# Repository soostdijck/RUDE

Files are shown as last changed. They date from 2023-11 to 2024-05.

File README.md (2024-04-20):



# Robak Unkillable Demon Edition

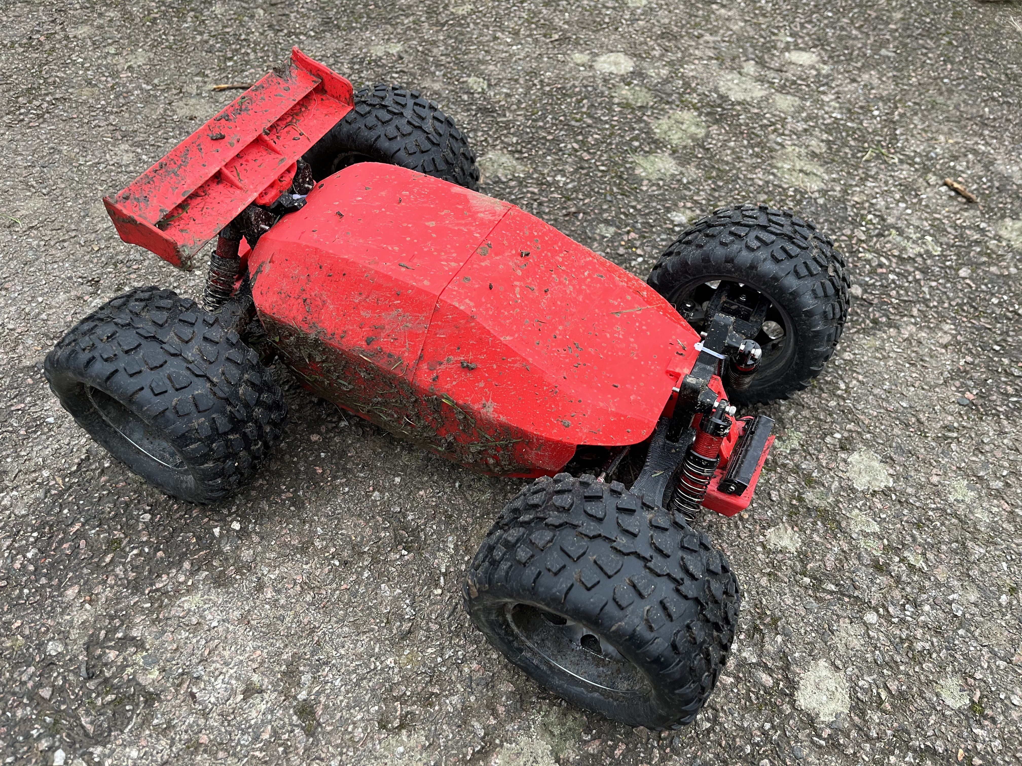
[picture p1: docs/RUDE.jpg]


Join the Discord (https://discord.gg/Cc8tsbZAE3)

An open-source RC car based on [Robak v2.2](https://github.com/robaki-dev/robak/).

The most resilient RC car on the planet! More driving and less repairing. This car only stops when your battery is empty. If you break this car after flying out of your apartment window I failed.

Select your own hardware with the BOM as your guide. All plastic parts can be 3D printed or bought from [my future webshop?]() (if you want to buy RUDE car parts, ask me in discord for now).

[Printing instructions](docs/printing.md)

[Bill Of Materials](docs/BOM.md)

[Assembly](docs/Assembly.md)

### FAQ: What is this car going to cost me?

Complete kit without plastic parts: Low budget: €200. Premium: €400. The BOM lists all premium parts.

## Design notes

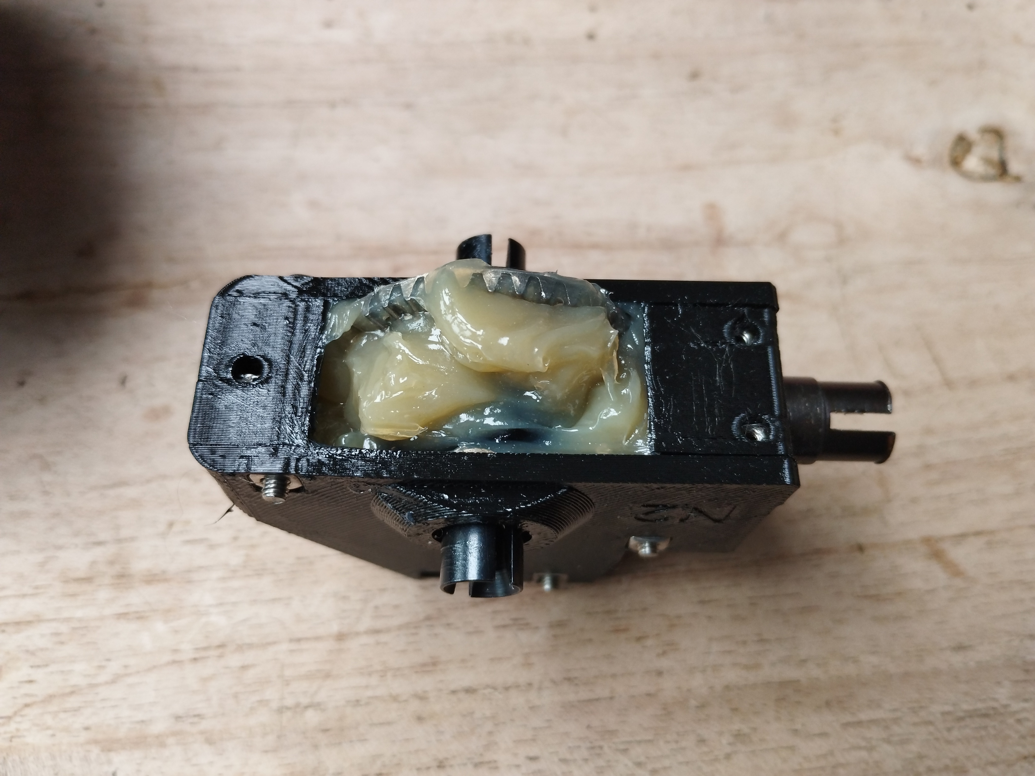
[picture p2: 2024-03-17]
docs/diff_housing_grease.jpg

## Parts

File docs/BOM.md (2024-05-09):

# BOM

Special attention to HSP 102011 and 2x190mm + 4x66mm ⌀5mm steel rods which are not included in stock Robak BOM. Also additional SHCS M3 + hex-nuts and 2x M5x40 bolts + square nuts are necessary if you come from Robak.

This car can handle much more power than Robak and is also heavier, I don't advise anything below 3S.

## Electronics

Part | Name | QTY | Notes
--- | --- | --- | ---
ESC + motor | 36xx or 42xx up to 82mm length | 1 | F.e. 3660 = 36mm diameter & 60mm length, 4278 = 42mm diameter & 78mm length.
ESC + motor | Hobbywing Ezrun MAX10 3665SD G3 2400KV + G2 140A ESC | 1 | Recommended. The newest Ezrun MAX8 & MAX10 sensored series are great. Get your Hobbywing electronics at a local shop, because aliexpress doesn't do warranty!
Battery for recommended MAX10 combo | 4S 4700mAh | 1 | https://s.click.aliexpress.com/e/_Dm7oLEB
RX + TX | DumboRC DDF-350 | X10FG or X6DCG | screen, lights/indicators support and with gyro https://s.click.aliexpress.com/e/_oCQUDqW (select M2 for metal steering wheel)
Servo | DS3240-180 or any other 180 deg variant | 1 | https://s.click.aliexpress.com/e/_DnBFawT
1:8 Motor | Ysido 4274 | 1 | Cheap but overpowered https://s.click.aliexpress.com/e/_DmBblkx NOTE: you need a 1:8 ESC for this. [has 6.5mm banana plugs instead of 4mm]
1:8 ESC | Hobbywing Quicrun 8BL150 | 1 | I use this in combination with the Ysido. Get your Hobbywing electronics at a local shop, because aliexpress doesn't do warranty!

## HSP

Part | Name | QTY | Notes
--- | --- | --- | ---
steering links | HSP 102011 | 2 | different from stock Robak
differential | HSP 02024 |2 | https://aliexpress.com/item/1178316591.html I recommend to get all your HSP parts from this store. Their quality seems to be superior. You can order, cancel payment, then ask seller to reduce the shipping costs.
front gear | HSP 02030 |1 |
rear gear | HSP 03015 |1 |e-clip shoud be included
cvd | HSP 108015 |4 |2 types available; more info on robaki.dev
5/6mm wheel hex | HSP 122042 |4 | https://s.click.aliexpress.com/e/_DnSrrOX depth depends a bit on the type of wheel. For the recommended wheels 5/6mm.
cups | HSP 02016 |2 |
servo link | HSP 02012 |1 |
steering links | HSP 06016 |1 |one pair
drive shaft | HSP 04003 |1 |
spur gear | HSP 11184 |1 |
pinion gear | HSP 11184 |1 | 29T ⌀3.175/5mm, check shaft of your motor. For weaker motors pick 21T.
ball head screw | HSP 02038 |4 |for steering
small bearings |5x10x4mm | 5pcs | https://s.click.aliexpress.com/e/_Ey7tCg3
big bearings |10x15x4mm | 4pcs | https://s.click.aliexpress.com/e/_oCNvIsS

### HSP must-have spares

Part | Name | QTY | Notes
--- | --- | --- | ---
differential | HSP 02024 | 2 |
front gear | HSP 02030 |1 |
rear gear | HSP 03015 |1 |e-clip shoud be included
cups | HSP 02016 |1 |
pinion gear | HSP 11184 |1 |⌀3.175/5mm, check shaft of your motor
grub screws | HSP 02099 |1 |
main gear pin | HSP 08027 |1 |
small bearings |5x10x4mm | 2 | 
big bearings |10x15x4mm | 2 | 

## Other

Part | Name | QTY | Notes
--- | --- | --- | ---
wheels | HSP 88005 | 4 | metal rims preferred since I have broken plastic rims before https://aliexpress.com/item/4000537479774.html [I haven't tried TPU wheels yet]
shocks |INJORA Aluminum Shock Absorber 100mm |4 | https://s.click.aliexpress.com/e/_EQmCy8T
battery straps |20mm width; 200mm long |2 |max width 25mm
DIY hinge pins |⌀5mm steel rod | 2x190mm + 4x66mm | https://s.click.aliexpress.com/e/_opSq9ew buying 500mm rods is best value [different from stock Robak]
sillicone oil (front & rear shocks) | 1000+ cSt | 20ml | this car's mass is >3kg so heavier oils preferred https://s.click.aliexpress.com/e/_ooUaPnU (very cheap, I'd recommend to buy both 2K and 1K)
sillicone oil (diffs) |80.000 cSt | 20ml |50.000-100.000 cSt will work https://s.click.aliexpress.com/e/_mKMass6 (from local shop is likely cheaper)
thread-locking fluid | | 10ml | Medium strength blue (cheap option: https://s.click.aliexpress.com/e/_mtYoqXC )
lithium grease | | 50ml |or any other grease for gears
CA glue / ZAP-RT | power glue | 20ml |tire glue (ZAP-RT for metal rims)

## Bolts

Part | Name | QTY | Notes
--- | --- | --- | ---
M5 Socket Head Screws | M5 SHCS 2x40 | | https://s.click.aliexpress.com/e/_mNYNVTc
M5 Square Nuts  | | 2 | https://s.click.aliexpress.com/e/_mKvxiiA
M3 Socket Head Screws | M3 SHCS 8x30 4x20 4x16 4x12 1x6 | | https://s.click.aliexpress.com/e/_mNYNVTc
M3 Flat Head Screws | M3 FHCS 30/25/20/16/12mm |20pcs each | https://s.click.aliexpress.com/e/_ontwkaW
M3 Thin Square Nuts  |DIN 562 |50 |ht. 1.8mm https://s.click.aliexpress.com/e/_mKvxiiA
M3 Nylon-Insert Locknuts |DIN 985; ISO 10511 |12 | for arm hinges https://s.click.aliexpress.com/e/_mKRqmKW
M3 General Purpose Washers |DIN 125; ISO 7089 |3 |motor mount to the plate https://s.click.aliexpress.com/e/_ooqqPiE
M4 Nylon-Insert Locknuts |DIN 985; ISO 10511 |4 |for wheels https://s.click.aliexpress.com/e/_mKRqmKW
M4 General Purpose Washers |DIN 125; ISO 7089 |4 |for wheels https://s.click.aliexpress.com/e/_ooqqPiE

## For stock body

Part | Name | QTY | Notes
--- | --- | --- | ---
M2x10mm Socket Head Screws |DIN 912; ISO 4762 |10 |bolt 2 body parts together https://s.click.aliexpress.com/e/_mKoi8nC 
M2 Nylon-Insert Locknuts |DIN 985; ISO 10511 |10 |bolt 2 body parts together https://s.click.aliexpress.com/e/_mKRqmKW
M8x60 bolt full thread |  |1 | Full Thread! To bolt rear body part to car. https://s.click.aliexpress.com/e/_EJMfISf 
M8 flange lock nut |  |1 | https://s.click.aliexpress.com/e/_Ew4tm55
M8 wing nut |  |1 | https://s.click.aliexpress.com/e/_EwzpS4j

## Tools

Part | Name | QTY | Notes
--- | --- | --- | ---
Worx electric screwdriver | WX242 | 1 | https://s.click.aliexpress.com/e/_msPBlN0 
Allen bits | H2 | 2 | https://s.click.aliexpress.com/e/_EuJdN3h or https://s.click.aliexpress.com/e/_msWyGcO

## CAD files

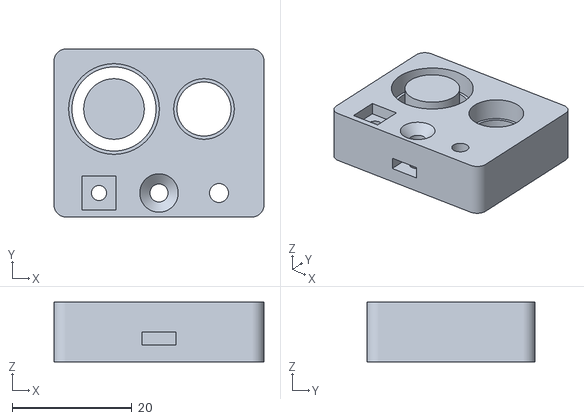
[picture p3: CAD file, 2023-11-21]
Calibration.stl
35.0 x 28.0 x 10.0

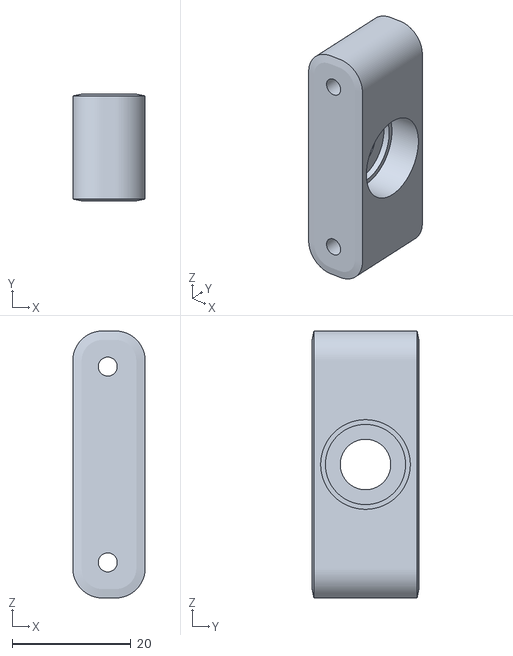
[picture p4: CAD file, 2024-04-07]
ROBAK_STL/CarrierHubR.stl
12.2 x 18.0 x 45.0

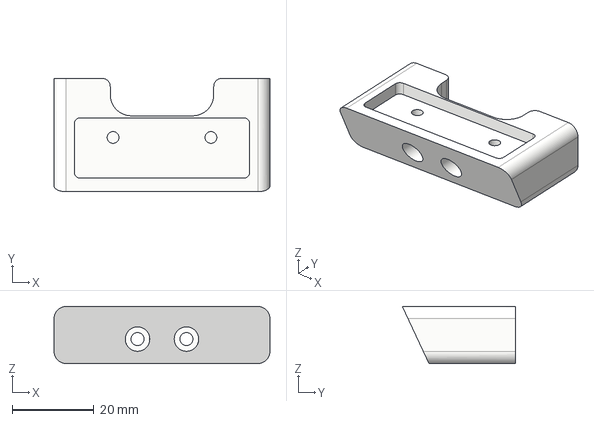
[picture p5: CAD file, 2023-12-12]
STEP/Braces/KNOG/Brace_KNOG.step
53.0 x 27.8 x 14.0 mm

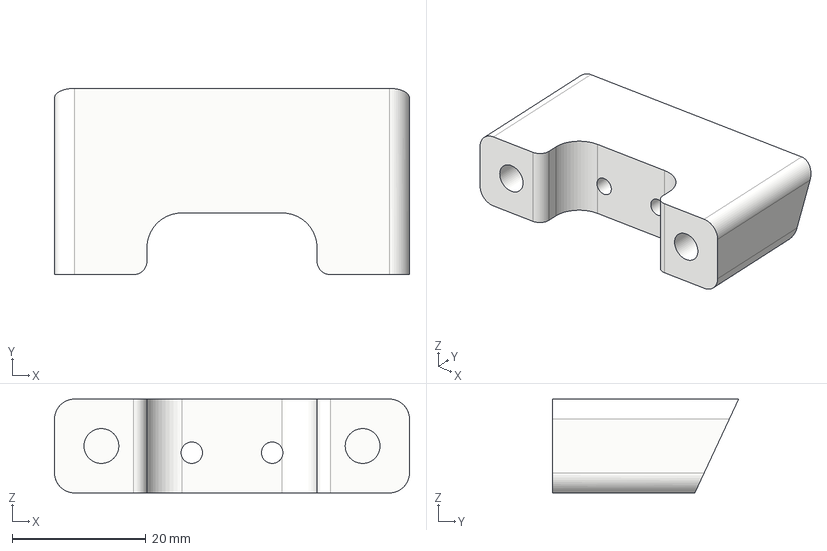
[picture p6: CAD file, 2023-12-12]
STEP/Braces/Stock/Brace.step
53.0 x 27.8 x 14.0 mm

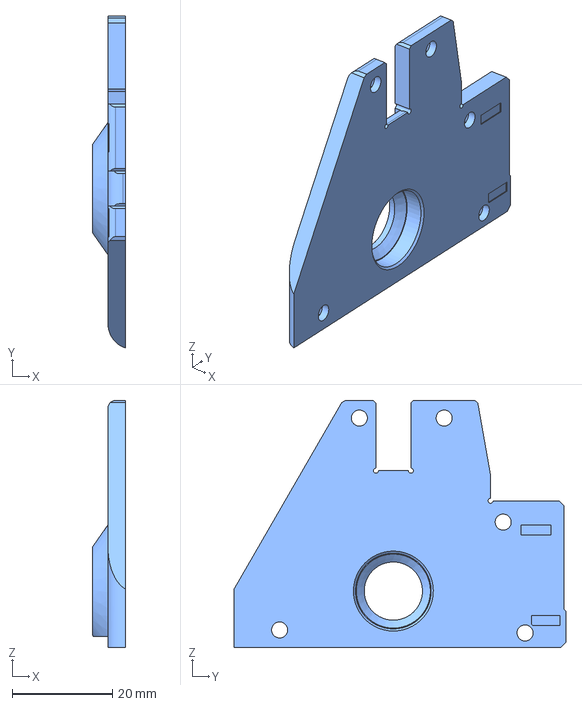
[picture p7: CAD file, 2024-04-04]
STEP/DiffCaseNutSide.step
6.51 x 66.2 x 49.3 mm

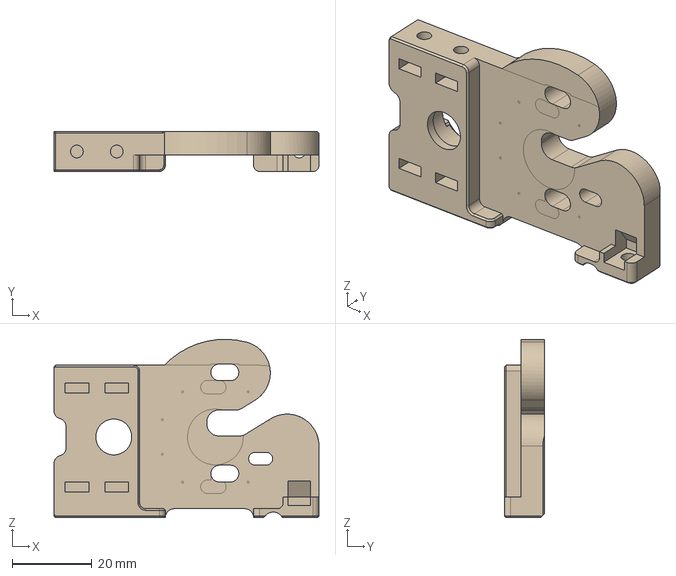
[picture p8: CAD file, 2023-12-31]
STEP/Motorplates/MotorPlate_42mm_MAX8.step
66.5 x 10.0 x 44.8 mm

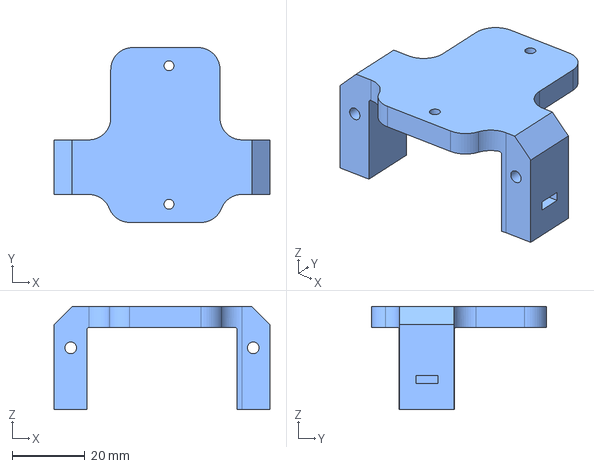
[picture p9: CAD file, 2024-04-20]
STEP/ServoMounts/Ezrun MAX10/ServoMount_EZRUN_MAX10.step
59.3 x 48.0 x 28.3 mm

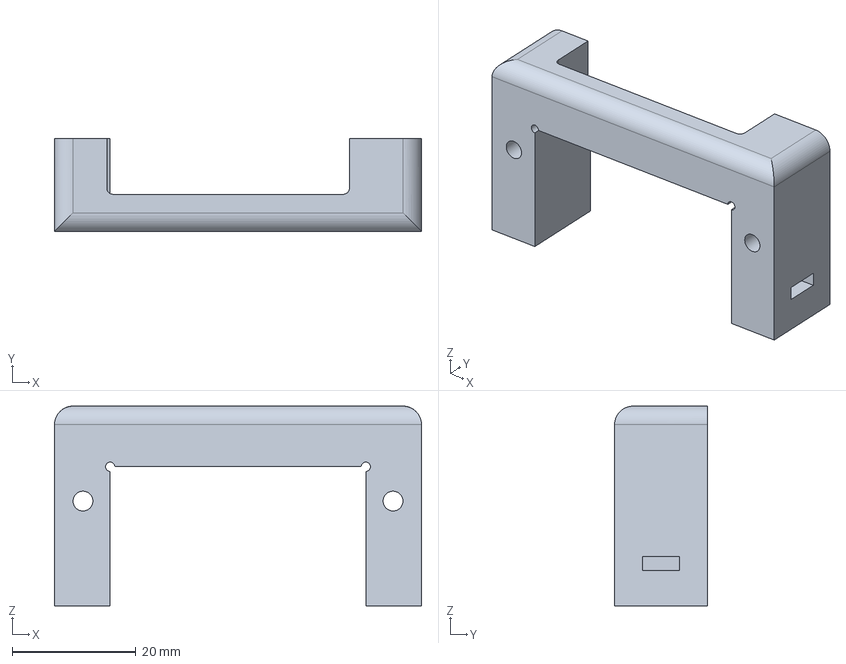
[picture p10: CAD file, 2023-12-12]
STEP/ServoMounts/Generic_1to10/ServoMount.step
59.3 x 15.0 x 32.3 mm

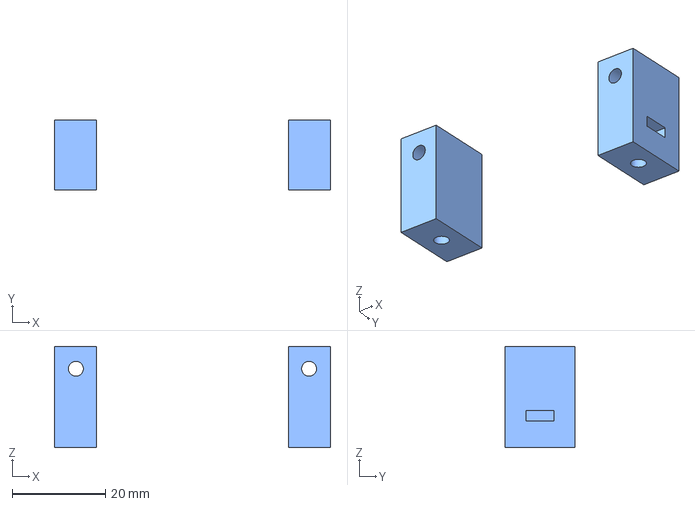
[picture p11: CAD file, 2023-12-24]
STEP/ServoMounts/Generic_1to8/ServoMount_bigESC.step
59.3 x 15.0 x 21.7 mm

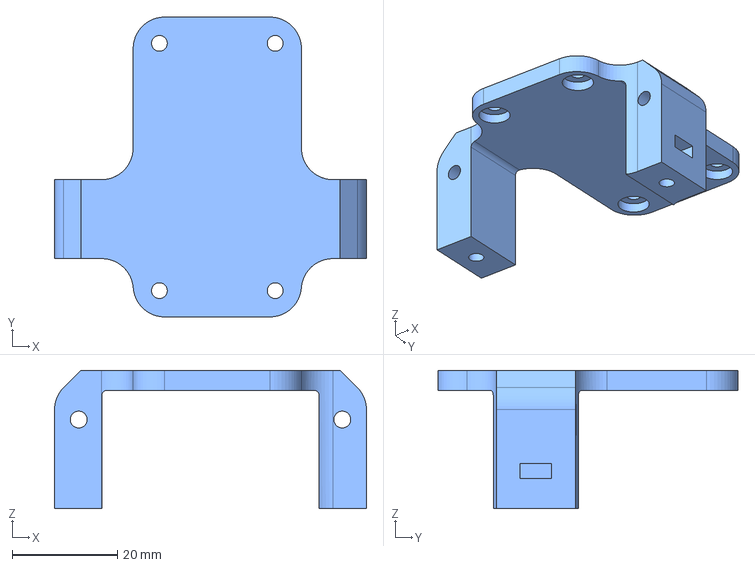
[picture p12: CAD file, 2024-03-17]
STEP/ServoMounts/Quicrun 8BL150/ServoMount_Quicrun8BL150.step
59.3 x 57.0 x 26.3 mm

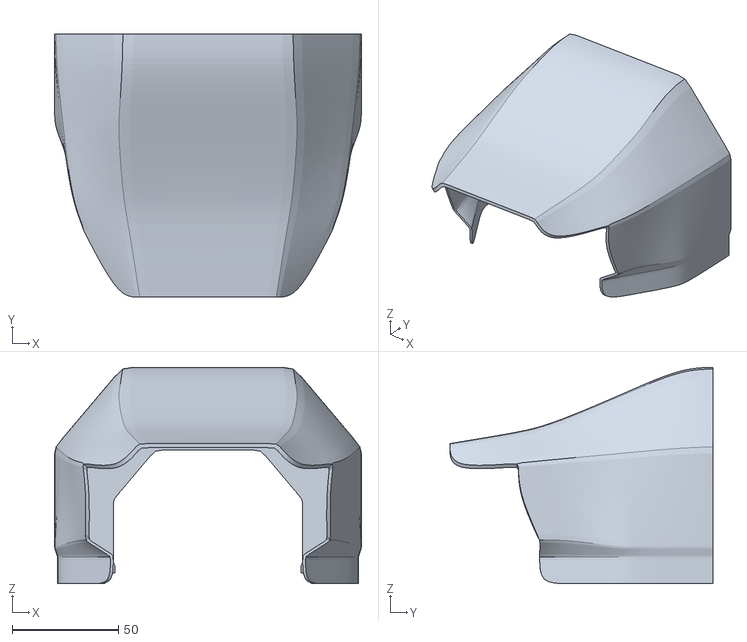
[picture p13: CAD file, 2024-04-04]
ROBAK_STL/BodyF.stl
144.8 x 124.1 x 102.0

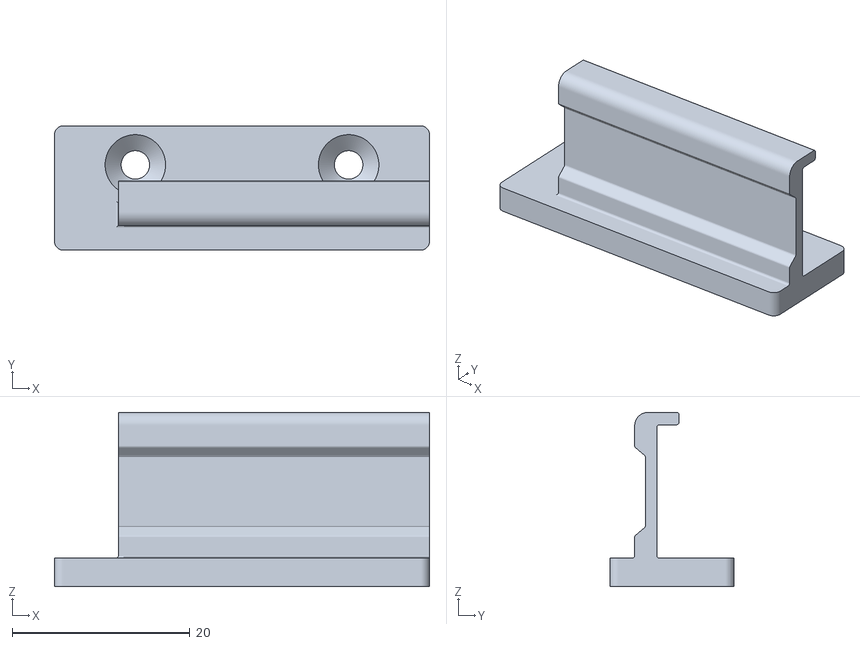
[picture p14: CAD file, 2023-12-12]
STEP/Braces/KNOG/LEDClip_KNOG.stl
42.2 x 14.0 x 19.6

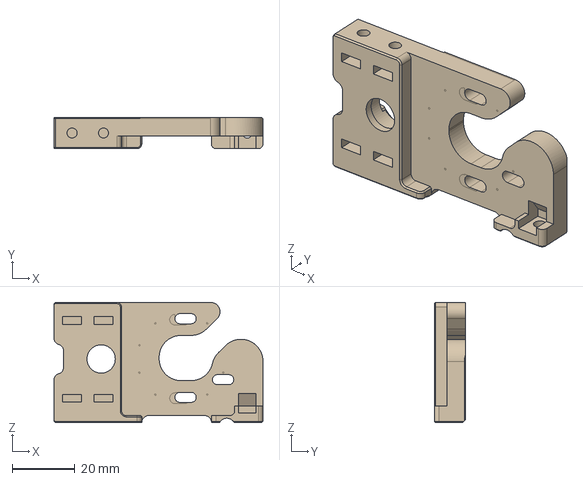
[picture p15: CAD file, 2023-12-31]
STEP/Motorplates/MotorPlate_36mm.step
66.5 x 10.0 x 38.3 mm

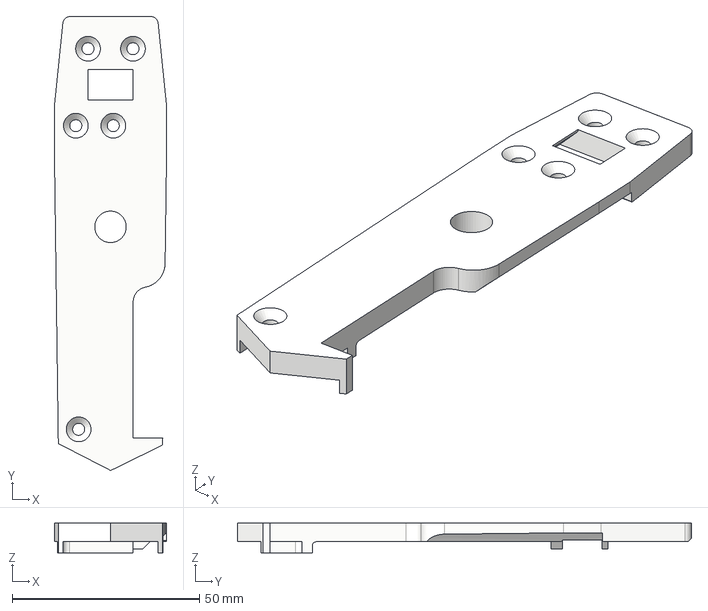
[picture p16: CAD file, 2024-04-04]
STEP/TopDeckR_longmotor_70-82mm.step
30.0 x 121.2 x 8.00 mm

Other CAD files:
ROBAK_STL/BodyR.stl
STEP/Motorplates/MotorPlate_42mm_ysido.step
STEP/TopDeckR.step
STEP/DiffCaseHeadSide.step
STEP/ArmFL.step
STEP/ArmFR.step
STEP/ArmRL.step
STEP/ArmRR.step
STEP/BellCrankL.step
STEP/BellCrankR.step
STEP/BodyF_Clip.step
STEP/BodyR_Clip.step
STEP/CarrierHubF.step
STEP/Chassis.step
STEP/Chassis_longmotor_70-82mm.step
STEP/DiffCaseCentralPart.step
STEP/HSP02016_insert.stl
STEP/Link.step
STEP/Motorplates/MotorPlate_blank.step
STEP/Outdated/BodyR_Clip.step
STEP/TopDeck.step
STEP/TopDeckF.step
STEP/TopDeckR_70-80mm_motor.step
STEP/Tower.step
STEP/UpperArmFL.step
STEP/UpperArmFR.step
STEP/UpperArmRL.step
STEP/UpperArmRR.step

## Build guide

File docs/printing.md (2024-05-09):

# Print settings

The chassis requires a 261x261 bed. In discord is a usermod available for 250x250 beds (cut corners) and another mod for 182x182 beds (split chassis).

Everything must be printed with 8 walls and 100% infill, unless otherwise noted.

Abrasive filaments are not weak but have worse layer adhesion. On the other hand CF/GF-filled TPU could be stiffer. More testing needs to be done to know what is best.

### Calibration

Make sure to print [this](/Calibration.stl) first for every filament to make sure your shrinkage is fine. As a reference: my TPU shrinkage is 99.8% and for ABS shrinkage 99.3%.

For quality prints I recommend this guide: https://ellis3dp.com/Print-Tuning-Guide/ basically walk through Tuning once and after that you only have to adjust PA and EM for different filaments and adjust first layer squish every now and then.

### Before printing TPU

Always dry your new TPU spool for a few hours in the oven at 60C. It's always wet from factory, which makes it hard to print and causes rough texture. If you use a new brand for the first time: set a low speed and set retraction to 0 mm, these can be experimentally increased (especially for harder TPU's) in consequent prints. You may need to do more adjustments but these are most important.

## PC

[For motorplate & bellcranks, ABS/ASA are fine too, but they are too weak for link/diffcase/servomount. PA deforms so Nylon is disrecommended.]

Part | Number | Support
--- | --- | ---
Link | 1 | Yes
MotorPlate | 1 | Yes
DiffCase | 2 | No
BellCranks | 1 | No
ServoMount | 1 | No

ServoMount may need adjustments for a specific ESC. Ezrun MAX10 and Quicrun 8BL150 are supported with bolted mounts. [Unverified but I suspect that Ezrun MAX8 has same mounting pattern as 8BL150 and that the Quicrun 10BL120 has same mounting pattern as MAX10.] Please share your custom mounts on discord.

## TPU 98A or harder

Note: TPU 95A is close in number but much more flexible than 98A and likely won't result in a good car.

Part | Number | Support
--- | --- | ---
Chassis | 1 | No
Arms | 1 | No
UpperArms | 1 | No
CarrierHubF | 2 | No
CarrierHubR | 2 | No
TopDeck | 1 | No
Tower | 2 | No
HSP02016_insert | 0-2 | No

Use a HSP02016_insert if your middle axis can (almost) escape. That one doesn't need to be TPU.

## TPU

2/3 walls and 0-40% infill (depends on hardness of your TPU, but a soft brace can absorb some impact).

Part | Number | Support
--- | --- | ---
Brace | 2 | No

# Stock body

## Any material

Avoid materials with weak layer adhesion. ASA/ABS bodies crack easily along the thin layer lines. In discord is a mod that includes a rear wing. BodyR_Clip has been removed in favor of an M8 bolt through TopDeckR, [see here](Assembly.md).

Part | Number | Support
--- | --- | ---
BodyF_Clip | 1 | No
Body | 1 | No

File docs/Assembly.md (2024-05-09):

## Assembly

At least loctite all grub screws + bolts going in the HSP steering links. Arms should be able to move freely, don't tighten the M3 bolts that function as joints.

[Info document](https://docs.google.com/presentation/d/1HM81BQhkKSFr_ZRTIKP950ZJcJBYzyWOIWn2UdTEApA/edit?usp=sharing) not everything is relevant for RUDE but its an informative read. RUDE uses new differential (diff) housings that should be a perfect fit for every good HSP 02024. There seems to be quite a quality difference between AliExpress vendors. All HSP parts from the store recommended in the BOM seems to last much longer. If your HSP diffs don't fit in the diff case well, consider buying theirs.

Install 190mm ⌀5mm steel rods through the two ⌀5mm holes in the sides of the chassis.

To make sure your diffs last as long as possible fill the inside ~80% with diff oil [50k-100k Cst]. Image below shows how it looks from factory (full of air, which is bad):
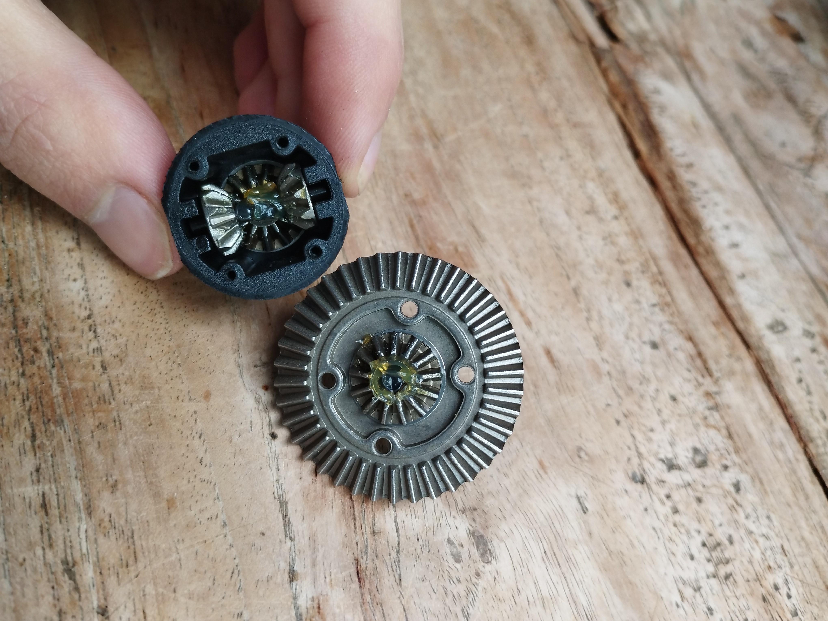
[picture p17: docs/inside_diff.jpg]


Also fill up the housing with grease, keep rotating until almost no grease wants to go in anymore, this will make your gears last as long as possible.

The steering link should be installed as follows (you may want to use the top hole on servo horn):
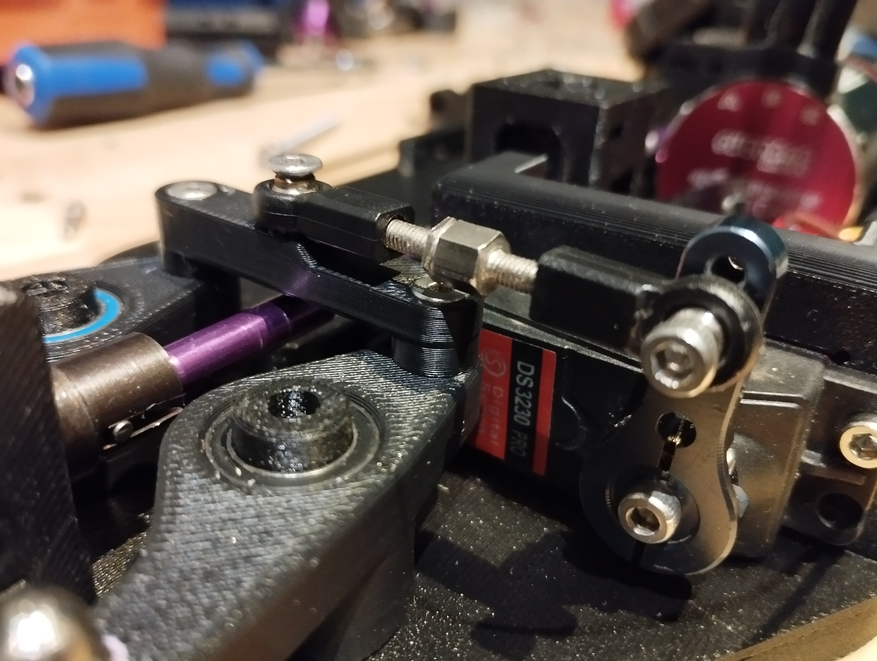
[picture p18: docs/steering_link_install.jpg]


The bearing in motorplate should be locked with a M3 washer + bolt (4mm). This way its possible to drive RUDE with RWD. The main reason for this feature is to protect your differential from damage when the middle axis escapes.
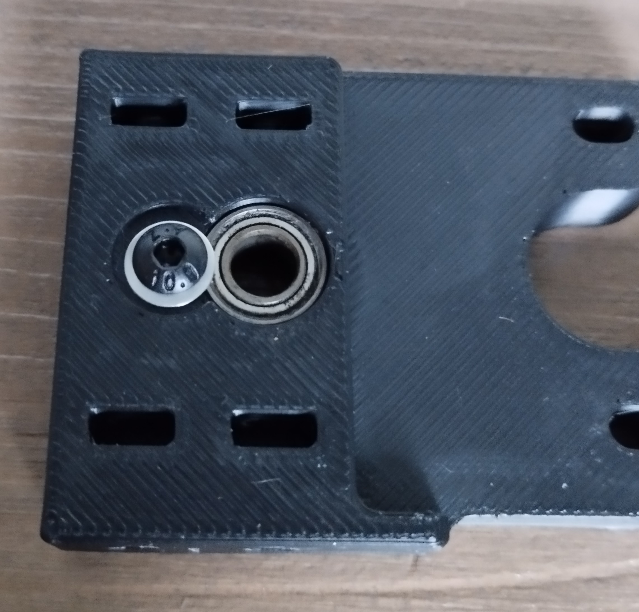
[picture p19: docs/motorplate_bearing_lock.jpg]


You need to drill a 8mm hole in the rear of the body, to fasten the body with a wing nut to the M8x60mm bolt that is coming out of TopDeckR.
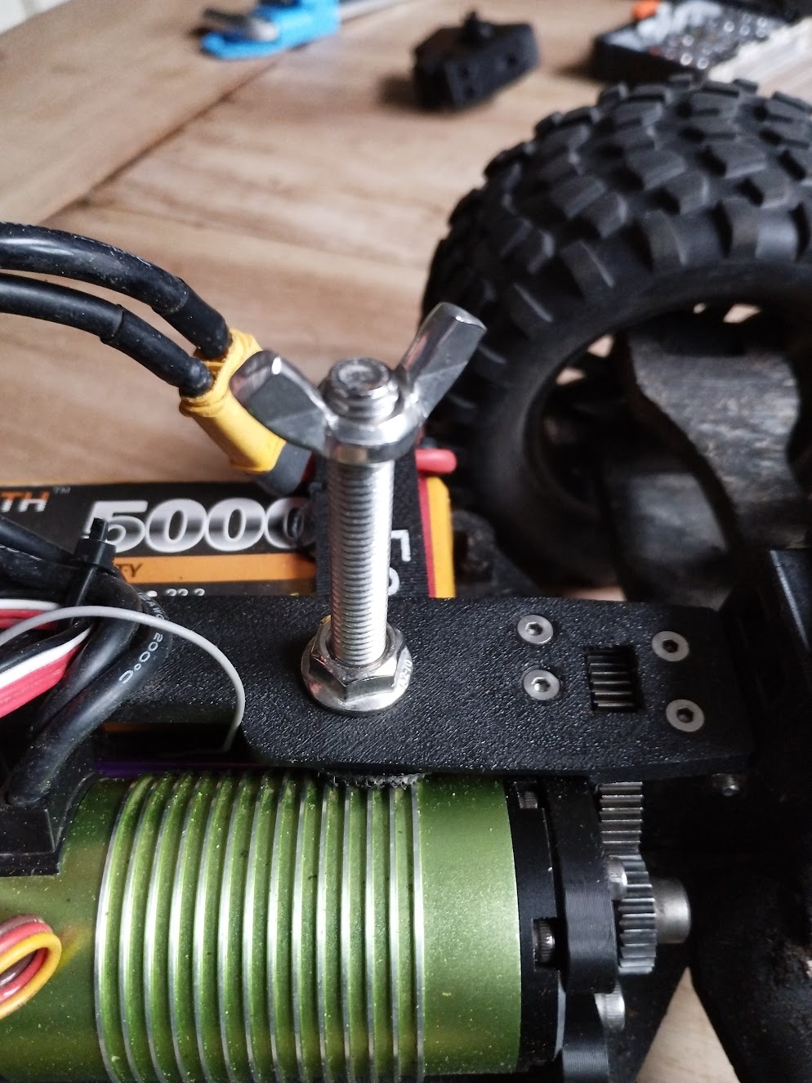
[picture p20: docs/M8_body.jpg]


Tires need to be glued to the rims, this needs to be waterproof so there is no water/dirt going inside the wheels, making your car harder to control. Power glue may suffice for plastic rims. ZAP-RT for metal.

For the rest assembly is pretty similar to [this video](https://www.youtube.com/watch?v=374VbFoaV5E).
Note: two M5x40 bolts are used for stiff steering. There are two big square holes in the bottom of the chassis for M5 square nuts.

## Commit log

2023-12-12 Initial release
    [ArmFL.step, ArmFR.step, ArmRL.step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]
2023-12-17 Update Tower.step
    Tougher towers
    [Tower.step]
2023-12-24 Initial release
    Up to 82mm motors
    [Chassis.step, Chassis_70-80mm_motor.step, Chassis_longmotor_70-82mm.step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]
2023-12-31 updated motorplates
    [MotorPlate_36mm.step, MotorPlate_42mm.step, MotorPlate_42mm_MAX8.step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]
2024-01-24 ezrun max10 mount added
    [ServoMount.step, ServoMount.stl, ServoMount_EZRUN_MAX10.step]
2024-02-04 minor fixes
    [HSP02016_insert.stl, ServoMount_EZRUN_MAX10.step]
2024-03-09 Update printing.md
    I couldn't find files with the previous names, I think these are the correct file names.
2024-03-17 docs update
    [ServoMount_Quicrun8BL150.step, hsp02024_diff_shim.step]
2024-04-04 RUDE diffs (and body update)
    [BodyF.stl, BodyR.stl, BodyR_Clip.step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]
2024-04-05 stiff filament section update
2024-04-07 CarrierHubR update
    [CarrierHubR.stl, HubCarrierR_ToeIn2.stl]
2024-04-20 Servomount ezrun MAX10 update
    [ServoMount_EZRUN_MAX10.step]
2024-04-28 bom update
2024-04-28 added more links to BOM
2024-05-06 updated BOM links

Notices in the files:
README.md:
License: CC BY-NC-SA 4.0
